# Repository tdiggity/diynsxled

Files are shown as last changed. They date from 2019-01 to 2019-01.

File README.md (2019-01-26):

# diynsxled

DIY LEDS for your NSX

# Prerequisites
1. A 3D printer is required to print the brackets and enclosure
2. A custom PCB can be made for about $30 from www.jlcpcb.com
3. [Install Arduino IDE](https://www.arduino.cc/en/Guide/HomePage)
4. Some soldering experience, or watch a few youtube videos first :)
5. Read this guide three times or more. There's a lot of info and if you're confused, open an issue above and I will try to help you out.

# Risks
The NSX taillights are old, and so there is a real risk that you'll break something. The bolts that connect to the car are fragile, the acrylic lenses are prone to cracking, etc. Just know that it's a real possibility that something can go wrong. Proceed at your own risk. 

Playing with high amperage is dangerous! Both tail lights on at full red brightness can use 5A. If you use White, even more. 

# Reading (optional)
* [NeoPixels UberGuide](https://learn.adafruit.com/adafruit-neopixel-uberguide/the-magic-of-neopixels)
* [Arduino bootloader](https://learn.sparkfun.com/tutorials/installing-an-arduino-bootloader/all) for instant start up time.

# 10,000 foot summary

The instructions below can be a bit overwelming. The high level steps are as follows:

1. Gather all the components, 3d printed parts and pcb.
2. Open tail lights and make cuts for led panels
3. Solder the pcb components
4. Wire the led together
5. Test led wiring
6. Wiring Harness - Car to PCB
7. Wiring Harness - PCB to LED Panels
8. Put brackets and leds in tail light
9. Test before sealing with car's wiring
10. Seal tail lights
11. Connect wiring

# Components

The component list links to websites for the number of items you would need to order. They are usually in sold in bundles and I have also listed the actual qty needed (if different) in case you can source these parts individually. For example, you need 6 diodes, but they only sell them in packs of 20.

If you're familiar with digikey and mouser, you can order a lot of these parts from there, too. However, some things were more expensive. 

### Custom Components
* Download the gerber zip file and send it to www.jlcpcb.com to get made. You get 10 for the same price, good if you mess up or for a group buy.
* Print the 3D printed parts in the `stl/` directory.
  * For tail light pieces, only drivers side is included. Use your slicer to mirror the brake and turn signal brackets for the passenger side. The reverse light bracket can be used on either side.
  * The parts are easy to print and do not require supports or anything special. 
  * Print with ABS. PETG should work, but ABS if you can.
  * In your slicer, split the parts up for the enclosure and print individually (and for bulb mount if using that).

### Amazon
* When installing LEDs, you'll get fast blinking turnsignals unless you use load resistors or the bulb sockets (both are listed as optional, pick one if you want regular speed blinking).
* The AVR programmer is optional, explained later on, but allows the Arduino to be programmed to wake up instantly without delay. 

|  Component | QTY | Actual QTY items needed | Notes |
| --- | --- | --- | --- |
|  [Pololu 5v regulator](https://www.amazon.com/Pololu-Step-Down-Voltage-Regulator-D24V90F5/dp/B01IGGR6TW?tag=diynsxled-20) | 1 |  |  |
|  [5mm terminals 2/3P pack](https://www.amazon.com/Gikfun-Terminal-Connector-Arduino-EK8365/dp/B015E3O4GS?tag=diynsxled-20) | 1 | 6x2pin, 2x3pin |  |
|  [2.5mm terminals 3P pack](https://www.amazon.com/Simpo-Terminal-300v10a-Drawing-Drawing/dp/B018OTAKJO?tag=diynsxled-20) | 1 | 28 |  |
|  [Capacitor](https://www.amazon.com/gp/product/B01DYJEHZ2?tag=diynsxled-20) | 1 |  |  |
|  [5A diode](https://www.amazon.com/gp/product/B079KCWPWQ?tag=diynsxled-20) | 1 | 6 |  |
|  [Resistors](https://www.amazon.com/gp/product/B072BL2VX1?tag=diynsxled-20) | 1 | 2x465, 5x4.7k, 5x1k |  |
|  [18ga Wire red](https://www.amazon.com/gp/product/B000HACYOS?tag=diynsxled-20) | 1 | optional if you have wire |  |
|  [18 ga Wire black](https://www.amazon.com/gp/product/B003J699RW?tag=diynsxled-20) | 1 | optional if you have wire |  |
|  [18 ga Wire green](https://www.amazon.com/gp/product/B003J65A84?tag=diynsxled-20) | 1 | optional if you have wire |  |
|  [18 ga wire pack](https://www.amazon.com/gp/product/B00N51OO7Q?tag=diynsxled-20) | 1 | optional if you have wire |  |
|  [Crimp tool](https://www.amazon.com/gp/product/B00OMM4YUY?tag=diynsxled-20) | 1 | optional, use with the cycle terminal crimps |  |
|  [Plug connectors](https://www.amazon.com/gp/product/B07DB7X9R9?tag=diynsxled-20) | 1 | optional | I prefer the ones from CycleTerminal, but you can also use these.|
|  [Benchtop DC power supply](https://www.amazon.com/gp/product/B071RNT1CD?tag=diynsxled-20) | 1 | optional, great for testing with or use a spare car battery |  |
|  [Socket adapters DIP](https://www.amazon.com/QLOUNI-122Pcs-2-54mm-Sockets-Adaptor/dp/B07CJ87NVT?tag=diynsxled-20) | 1 | Optional [1x6pin, 1x16pin] | For chips from digikey |
|  [Stacking headers for Nano](https://www.amazon.com/Shield-Stacking-Header-Arduino-Pack/dp/B0756KRCFX?tag=diynsxled-20) | 1 |  |  |
|  [Arduino Nano (Brand name)](https://www.amazon.com/Arduino-A000005-ARDUINO-Nano/dp/B0097AU5OU?tag=diynsxled-20) | 1 | optional (pick this or 3rd party) | Brand name. 3rd party just as good.|
|  [Arduino Nano (china)](https://www.amazon.com/ATmega328P-Microcontroller-Board-Cable-Arduino/dp/B00NLAMS9C?tag=diynsxled-20) | 1 | optional  |  |
|  [AVR Programmer](https://www.amazon.com/gp/product/B004G54E9I?tag=diynsxled-20) | 1 | Optional |  |
|  [Turn Signal Bulbs](https://www.amazon.com/gp/product/B07DFYSM5J?tag=diynsxled-20) | 1 | Optional |  |
|  [Load resistor](https://www.amazon.com/Resistors-Signal-License-Warning-Cancellor-x/dp/B004EDF8HY/ref=sr_1_8?tag=diynsxled-20) | 1 | Optional |  |
|  [5 wire connector](https://www.amazon.com/Wago-222-415-LEVER-NUTS-Conductor-Connectors/dp/B07CN5974J?tag=diynsxled-20) | 1 | 5, optional | There are better ways to splice wires |  
|  [Morimoto Butyl](https://www.amazon.com/RetroRubber-Grade-Butyl-Headlight-Sealant/dp/B01N5PM29J?tag=diynsxled-20) | 1 |  |  |
|  [M2/M3 bolts and nuts](https://www.amazon.com/gp/product/B07CSSVRPL?tag=diynsxled-20) | 1 | 6xM2, 10xM3 |  |
|  [Jumper wires](https://www.amazon.com/gp/product/B005TZJ0AM?tag=diynsxled-20) | 1 | optional | These will make wiring the panels together easier. We only need the short 4.7in ones.. |

**Note that the Amazon links have an affiliate link attached to them. This helps me recoupe some of the cost of development, and future dev work.* 

### Digikey
|  Component | QTY Needed | Actual items needed | Notes |
| --- | --- | --- | --- |
|  [Pin headers for Pololu regulator](https://www.digikey.com/products/en?mpart=TSW-202-07-T-S&v=612) | 2 |  |  |
|  [Opto 4ch](https://www.digikey.com/product-detail/en/PS2501-4-A/PS2501-4A-ND/770687) | 1 |  |  |
|  [Opto 2ch](https://www.digikey.com/product-detail/en/4N35/4N35-ND/1738522) | 1 |  |  |

### Aliexpress
* The LED panels are cheapest on Aliexpress. With regards to quality issues, I feel that all the panels i've bought have for the most part been great. Only 2 died on me, and I think that had more to do with me than them. In any case, purchasing extras might be good insurance since they take awhile to ship. 
* In total, you need 14 panels, 65mm square. The name branded NeoPixel panels from AdaFruit are 71mm.....do not use those unless you want to update the STL files.
* The White panels are used for the reverse light area. You can opt to use all black led panels, too.

|  Component | QTY Needed | Actual items needed | Notes |
| --- | --- | --- | --- |
|  [White LED panels](https://www.aliexpress.com/item/WS2812B-8x8-64-Bit-Full-Color-5050-RGB-LED-Lamp-Panel-Light-for-Arduino-OS857/32822265747.html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) | 2 |  |  |
|  [Black LED panels](https://www.aliexpress.com/item/WS2812-LED-5050-RGB-8x8-64-LED-Matrix-for-Arduino/32622872541.html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) | 12 |  |  |

### Cycle Terminal
These connectors connect to the OEM connectors for a really clean install. The optional parts are used in place of using a bulb socket adapter to wire things up. This is explained later on, but I recommend getting these optional components because it makes things more compact. 

|  Component | QTY Needed | Actual items needed | Notes |
| --- | --- | --- | --- |
|  ET250-4 Male | 1 |  | (OEM Acc power) |
|  HD 090-2 Male | 2 |  | (OEM Turn signal) |
|  HD 090-8 Male | 1 |  | (OEM main wiring) |
|  HD 090-6 Female | 1 |  | (OEM brake lamp defeat) |
|  3 pin HD 090  Female Connector | 6 | Optional | (data lines) |
|  3 pin HD 090  Male Connector | 6 | Optional | (data lines) |
|  2 pin HD 090  Female Connector | 4 | Optional | (power lines) (same as TS) (voltage drop) |
|  2 pin HD 090  Male Connector | 4 | Optional | (voltage drop) |

# Opening up your tail lights
Search google for opening up your tail light housing. You'll need to remove the gasket and electrical wiring and brake lamp detector box. 

# Tail Light Prep
You need to make these cuts to your tail lights. They are not visible if you decide to revert back to stock:

1. In the brake light area, there is a strip of plastic that comes flush to the rest of the light. This needs to be cut down. 
2. Next to the strip that you just cut, you'll need to make a small hole for the screw terminal to fit through. Save this step for when you test fit the 3d printed brackets and leds. 
3. Reverse light area, make two cuts so let the led panel sit flush.
tbd - include images of cuts

Next:
1. Remove the reflectors in the brake, reverse, and turnsignal areas.
2. You can keep all the diffusers.
3. you will not reuse the inner clear panel that is on the brake lamp area.

# LED Panel Prep
### soldering
Solder the two 3-pin 2.54mm terminals to each panel. 
tbd - image

### panel orientation and prep
The order of the panels goes from reverse light to brake lights to turn signals.
1 reverse light panels
5 brake lights panels
1 turn signal panels

For the 5 brake light panels, you need to glue the ends together. Each panel has an input terminal and output terminal. You want to glue them together so that the output terminal of one panel is next to the input terminal of another. 

tbd see image

# PCB Soldering

The holes will guide you. If it doesn't fit, you have the wrong part. 

Misc notes:
1. 5mm pins are used with the biggest holes in the voltage regulator. Only the center two on each end need to be soldered. 
2. The DIP sockets on the two chips are optional, but allow you to change the chips out if they get damaged without having to desolder everything. 
3. The nano uses header pins to easy connect and disconnect. There are 15 pins on each side. On my board, I only had 14 pin stacking headers, so my last row of pins near the usb is not used but that's ok because no connections are there. 
4. PCB uses M2 screws to mount to enclosure. 

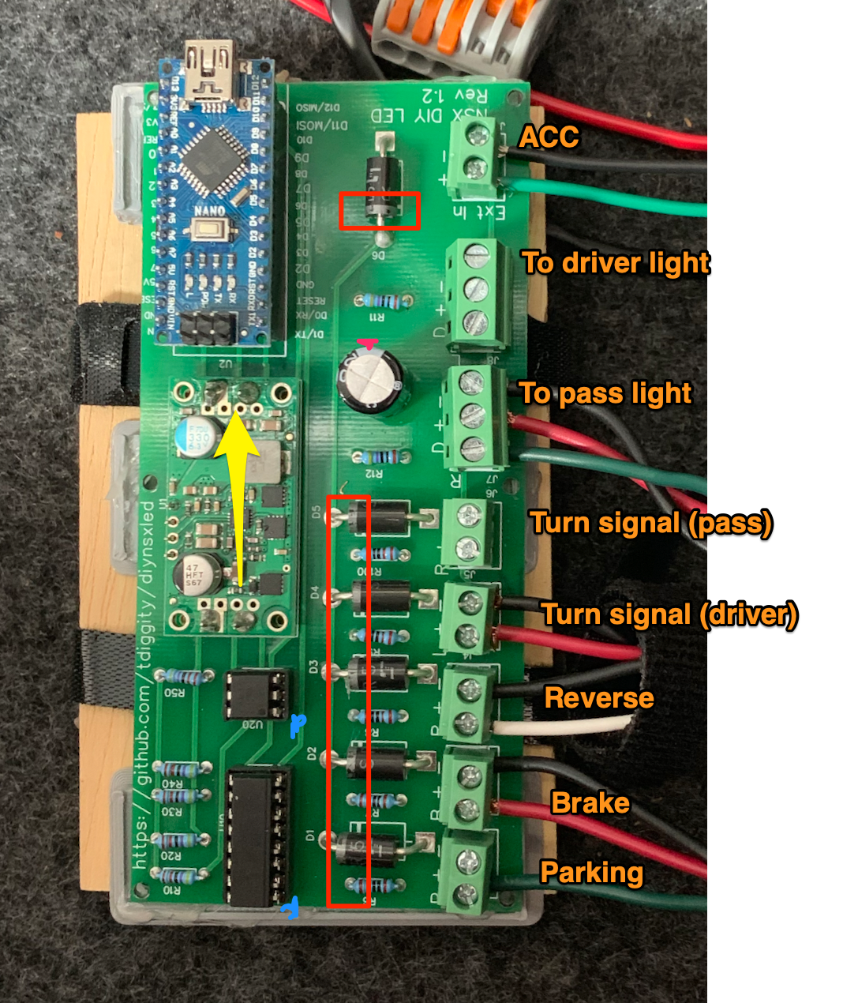
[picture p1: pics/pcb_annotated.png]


Notes about image:
* Red boxes - Diode orientation matters
* Red dot - Note grey strip on capacitor
* Blue dots - These note pin 1 of the chip, usually a notch or dot on the chip
* Yellow arrow - Voltage In to Voltage Out

tbd - insert resistor diagram here
Resistors
* 465 ohm - R11, R12
* 1k ohm - R10, 20, 30, 40, 50
* 4.7k ohm - R6, R7, R8, R9, R100

# Wiring guide
## LED panels
tbd
* Note, the white panels are labeled backwards, probably!

## PCB to LEDs
tbd 
## Car to PCB
tbd

# Test fit parts in tail lights
Test mount the 3d printed brackets in the tail light with the led panels. Ensure that the panels fit flush. They should slide in easily. If not, you might need to shave off some more of the cuts you previously made. 

If everything fits, first glue the 3d printed brackets to the tail lights with some superglue and/or hot glue. Once that sets, use hotglue on the tabs and attach the led panels. Super glue and hot glue don't conduct electricity.

Tip: Ensure that the brackets are flush with the border of the tail lights. Hot glue sets quickly enough for you to get them  lined up well. 

# Loading the arduino code
For testing - open the test file in the `test/` folder and upload it using the arduino IDE. 
For driving use - open the diynsxled.ino file and upload it using the arduino IDE. 

### Advanced - use the AVR programmer to load the code
The Arduino is only on when the key is in ACC position (2nd key position and also when engine is on). Otherwise it is off and not using any power.

In stock form, it takes about 1-2 seconds before any code can be run when first powering up. WHen the car is running, the Arduino is always on, so there is no worry of delay. 

When the Arduino is off, the LEDS will not work correctly in certain cases because the arduino does not have power long enough to get past the startup stage:
* When the emergency lights are on
* If you have a security system that blinks the leds upon activation/deactivation. 

This can be fixed by using an [AVR programmer](https://www.amazon.com/gp/product/B004G54E9I?tag=diynsxled-20) to remove the 1-2 second delay and instantly execute the LED program. Follow the instructions here: [AVR Guide](https://learn.sparkfun.com/tutorials/pocket-avr-programmer-hookup-guide/all) (pay attention to the "Programming with Arduino" section.)

# Testing (pre-flight)
Load the test code in the `tests/` folder. The first time you run the test code, let them run for a few hours or overnight. If you're using the [Benchtop DC power supply](https://www.amazon.com/gp/product/B071RNT1CD?tag=diynsxled-20), this won't be a problem. If using a car battery, i'm not sure how long they will last. But something is better than nothing. It's been said that if an electrical thing will fail, it'll fail earlier rather than later. 

It's advised to do testing at various stages to check your wiring:
* After all terminals and wires soldered, but before glueing panels together
* After brake panels are glued together
* After mounting into taillights but before sealing
* After sealing

# Sealing your lights
Use morimoto butyl

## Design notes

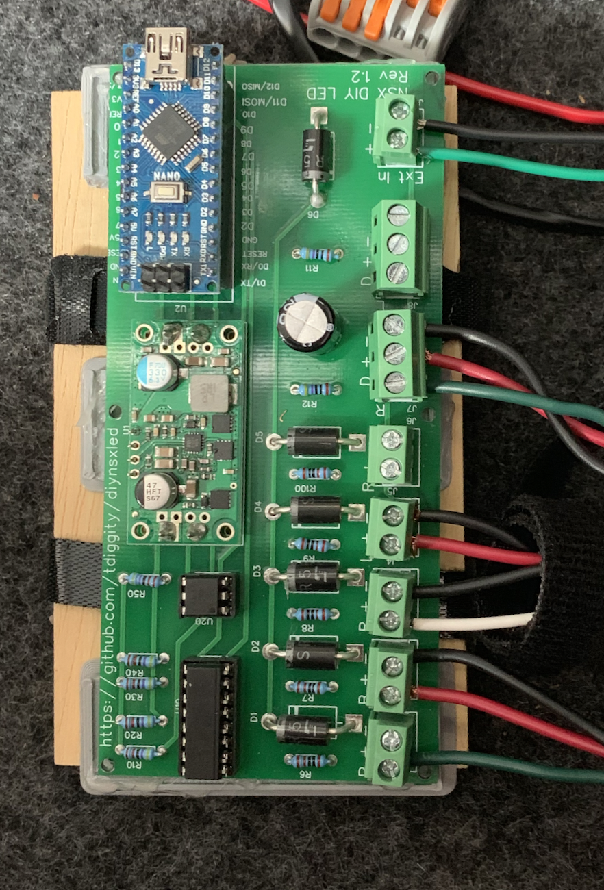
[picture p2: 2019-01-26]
pics/pcb.png

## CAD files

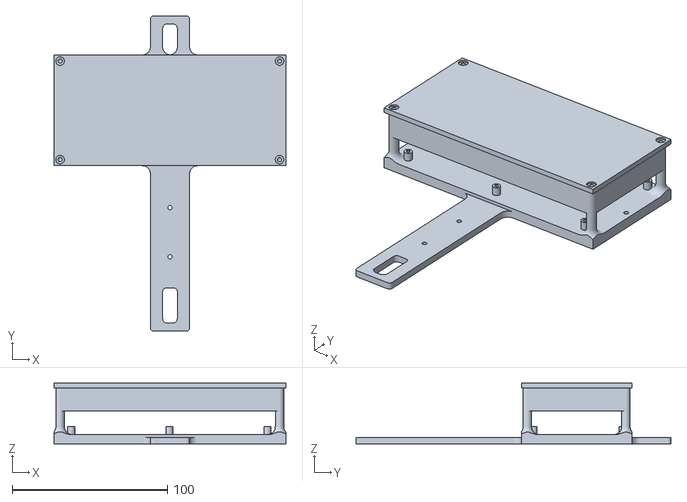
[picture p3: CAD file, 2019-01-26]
stls/enclosure/enclosure_plus_bracket.stl
149.5 x 203.0 x 39.0

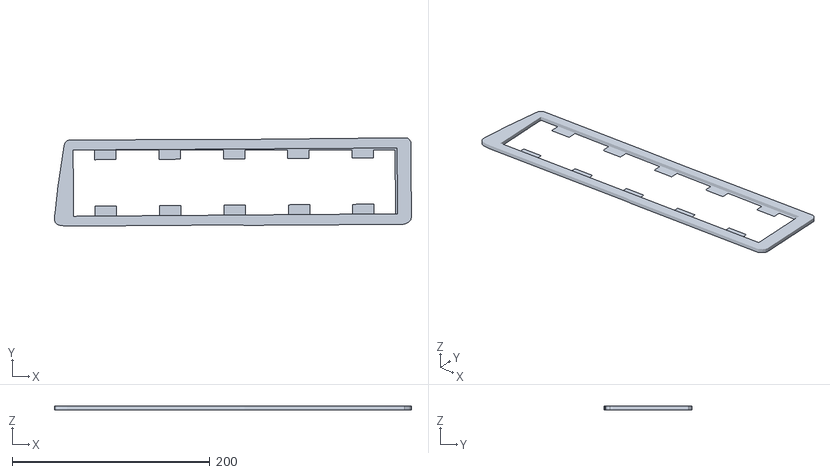
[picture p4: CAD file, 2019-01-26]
stls/taillights/Tail Lights - Brake Lights (Driverside).stl
361.5 x 89.5 x 4.00

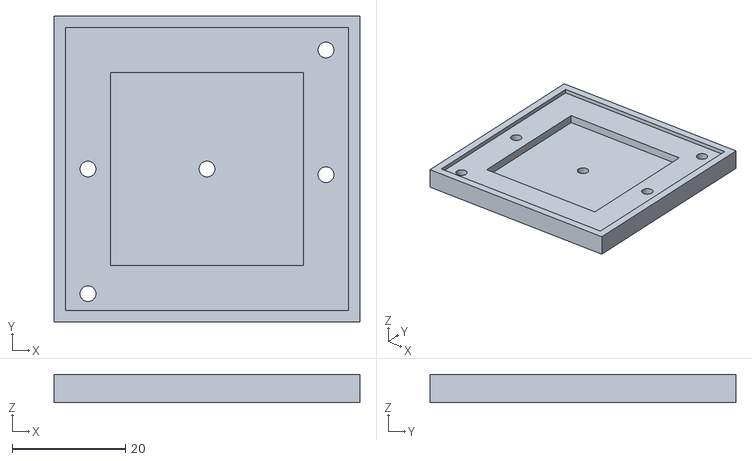
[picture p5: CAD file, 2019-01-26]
stls/enclosure/load_resistor_mount.stl
54.0 x 54.0 x 5.00

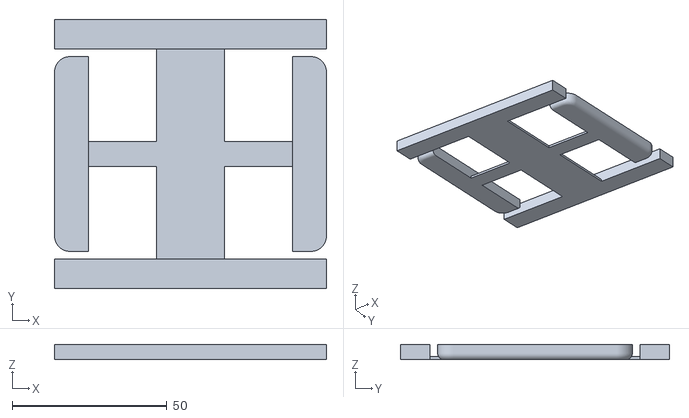
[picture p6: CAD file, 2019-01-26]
stls/taillights/Reverse Light.stl
88.0 x 87.0 x 5.00

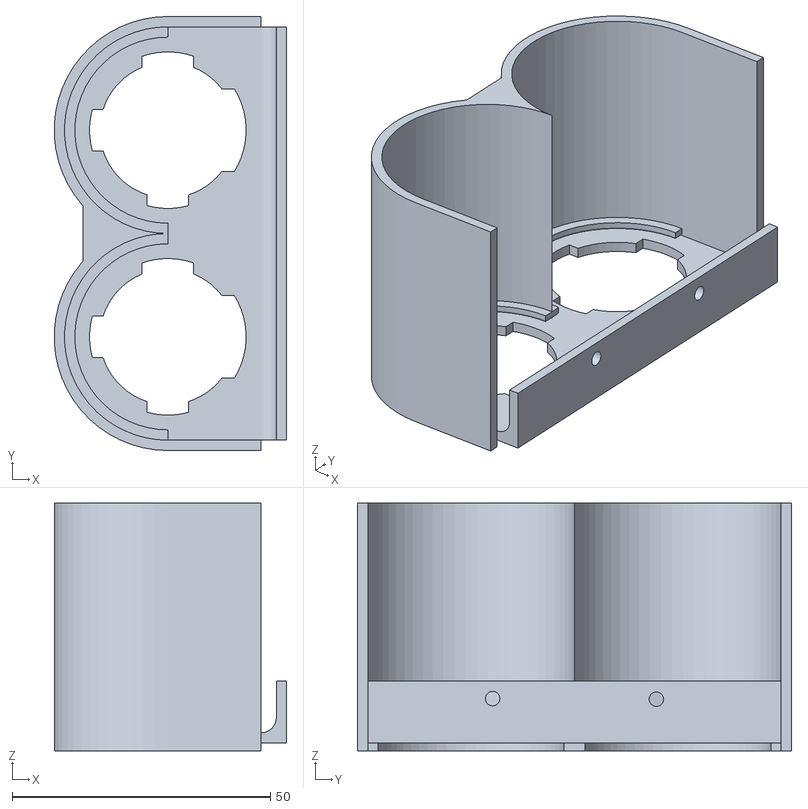
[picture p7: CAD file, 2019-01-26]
stls/enclosure/bulb_mount.stl
45.0 x 84.0 x 48.0

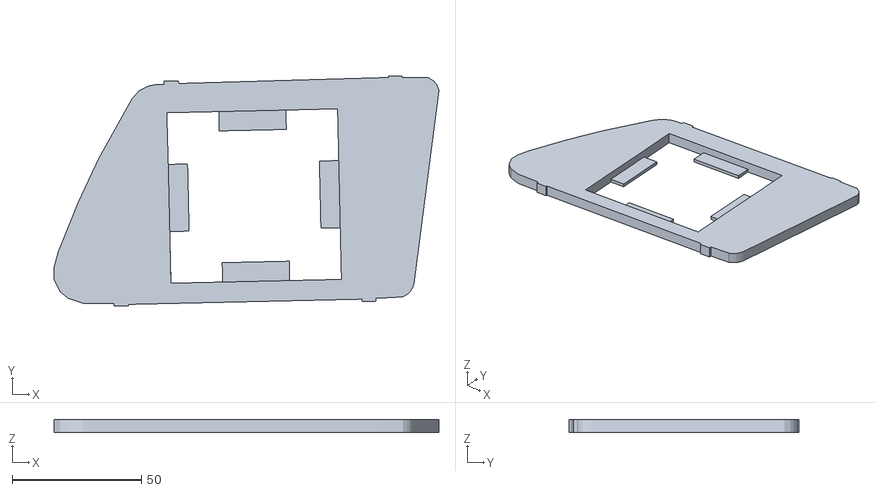
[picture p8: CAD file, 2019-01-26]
stls/taillights/Turn signal (Drivers side).stl
149.0 x 89.1 x 5.00

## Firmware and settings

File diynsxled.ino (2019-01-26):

/*
   LED Tail lights for NSX
   All rights reserved
   Intended for off-road use only
*/

#include <Adafruit_GFX.h>
#include <Adafruit_NeoMatrix.h>
#include <Adafruit_NeoPixel.h>
#include <MemoryFree.h>
#ifndef PSTR
#define PSTR // Make Arduino Due happy
#endif

// Data output pins
#define PASSENGER_MATRIX_PIN  5   // passenger side
#define DRIVER_MATRIX_PIN     6   // passenger side

// Opto-isolator inputs
#define OPTO_IN_PARKING       7   // parking
#define OPTO_IN_BRAKES        8   // brakes
#define OPTO_IN_REVERSE       9   // reverse
#define OPTO_IN_DRIVER_TS     10  // driver turn signal
#define OPTO_IN_PASSENGER_TS  11  // passenger turn signal

// Color definitions - only used for black because you can't set
// brightness on these without changing them all.
#define BLACK    0x0000
#define RED      0xF800
#define ORANGE   0xFC60
#define WHITE    0xFFFA
#define BLUE     0x001F

// brightness_levels
#define BRAKE_BRIGHTNESS    220
#define PARKING_BRIGHTNESS  125
#define TS_BRIGHTNESS       220
#define REVERSE_BRIGHTNESS  125

// default state of optocoupler inputs
int pinState_driver_ts = 0;
int pinState_passenger_ts = 0;
int pinState_reverse = 0;
int pinState_parking = 0;
int pinState_brake = 0;

// for determining what leds to turn on
boolean brakesOn = false;
boolean parkingOn = false;
boolean driverTurnsignalOn = false;
boolean passengerTurnsignalOn = false;
boolean reverseOn = false;

void setup() {
  pinMode(OPTO_IN_PARKING,      INPUT_PULLUP);
  pinMode(OPTO_IN_BRAKES,       INPUT_PULLUP);
  pinMode(OPTO_IN_REVERSE,      INPUT_PULLUP);
  pinMode(OPTO_IN_DRIVER_TS,    INPUT_PULLUP);
  pinMode(OPTO_IN_PASSENGER_TS, INPUT_PULLUP);
  pinMode(LED_BUILTIN,          OUTPUT);        // turn on if there's an error
  //Serial.begin(115200);
  Serial.println("starting");
}

void loop() {
  // get state of what lights should be on
  pinState_parking      = digitalRead(OPTO_IN_PARKING);
  pinState_brake        = digitalRead(OPTO_IN_BRAKES);
  pinState_reverse      = digitalRead(OPTO_IN_REVERSE);
  pinState_driver_ts    = digitalRead(OPTO_IN_DRIVER_TS);
  pinState_passenger_ts = digitalRead(OPTO_IN_PASSENGER_TS);
  delay(1); // delay in between reads for stability

  Serial.print("freeMemory()=");
  Serial.println(freeMemory());

  // analyze the state of lights
  // brake lights take priority over parking lights.
  if (pinState_brake == 1) {
    brakesOn = true;
    parkingOn = false;
  } else if (pinState_parking == 1) {
    parkingOn = true;
    brakesOn = false;
  } else {
    brakesOn = false;
    parkingOn = false;
  }

  //reverse lights
  if (pinState_reverse == 1) {
    reverseOn = true;
  } else {
    reverseOn = false;
  }

  //left turnsignal
  if (pinState_driver_ts == 1) {
    driverTurnsignalOn = true;
  } else {
    driverTurnsignalOn = false;
  }
  
  //right turnsignal
  if (pinState_passenger_ts == 1) {
    passengerTurnsignalOn = true;
  } else {
    passengerTurnsignalOn = false;
  }


  // we do it this way because there isn't enough memory if you make the neopixels global.
  setLeds(brakesOn, parkingOn, reverseOn, passengerTurnsignalOn, PASSENGER_MATRIX_PIN);
  setLeds(brakesOn, parkingOn, reverseOn, driverTurnsignalOn, DRIVER_MATRIX_PIN);
}

void setLeds(boolean brakesOn, boolean parkingOn, boolean reverseOn, boolean turnsignalOn, 
              int pin) {

  unsigned long startTime = millis();
  // Matrix objects
  Adafruit_NeoMatrix matrix = Adafruit_NeoMatrix(
                                8, 8, // pixel width/height per matrix
                                7,    // number of tiles
                                1,    // width of tiles
                                pin,
                                NEO_MATRIX_TOP     + NEO_MATRIX_LEFT +
                                NEO_MATRIX_ROWS    + NEO_MATRIX_PROGRESSIVE,
                                NEO_GRB            + NEO_KHZ800);
  matrix.begin(); // init matrix
  
  if (brakesOn) {
    // only show 2 beause that's how stock setup does it
    //matrix.fillRoundRect(8,  0, 12, 8, 1, matrix.Color(BRAKE_BRIGHTNESS, 0, 0));
    matrix.fillRoundRect(22, 0, 12, 8, 1, matrix.Color(BRAKE_BRIGHTNESS, 0, 0));
    matrix.fillRoundRect(36, 0, 12, 8, 1,matrix.Color(BRAKE_BRIGHTNESS, 0, 0));
  } else if(parkingOn) {
    matrix.fillRoundRect(8,  0, 12, 8, 1, matrix.Color(PARKING_BRIGHTNESS, 0, 0));
    matrix.fillRoundRect(22, 0, 12, 8, 1, matrix.Color(PARKING_BRIGHTNESS, 0, 0));
    matrix.fillRoundRect(36, 0, 12, 8, 1, matrix.Color(PARKING_BRIGHTNESS, 0, 0));
  }

  if (reverseOn) {
    matrix.fillRect(0, 0, 8, 8, matrix.Color(REVERSE_BRIGHTNESS, REVERSE_BRIGHTNESS, REVERSE_BRIGHTNESS));
  }

  if (turnsignalOn) {
    matrix.fillRoundRect(48, 0, 8, 8, 1, matrix.Color(TS_BRIGHTNESS, 0, 0));
  }

  matrix.show();
  Serial.print("P ");
  Serial.print(parkingOn);
  Serial.print(" B ");
  Serial.print(brakesOn);
  Serial.print(" R ");
  Serial.print(reverseOn);
  Serial.print(" TS ");
  Serial.print(turnsignalOn);
  Serial.print(" PIN ");
  Serial.print(pin);
  Serial.print(" Matrix: freeMemory()=");
  Serial.print(freeMemory());
  unsigned long currentTime = millis();
  unsigned long elapsedTime = currentTime - startTime;
  Serial.print("\t Time to calculate: ");
  Serial.println(elapsedTime);

  // if it takes more than 100ms to calculate what leds to show, then turn on the led!
  if (elapsedTime > 100) {
    digitalWrite(LED_BUILTIN, HIGH);
  }
}

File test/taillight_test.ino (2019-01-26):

/*
 * Test code for DIYNSXLED
 * Use with one side only
 * Insert the 3 wires into the passenger out
 * Add power to the ACC 2-pin port
 * Run this code and it will cycle through the lights in this order: Parking, brake, reverse, turn signal.
 */

#include <Adafruit_GFX.h>
#include <Adafruit_NeoMatrix.h>
#include <Adafruit_NeoPixel.h>
#ifndef PSTR
  #define PSTR // Make Arduino Due happy
#endif

// Data output pins
#define PASSENGER_MATRIX_PIN  5   // passenger side

// Opto-isolator inputs
#define OPTO_IN_PARKING       7   // parking
#define OPTO_IN_BRAKES        8  // brakes
#define OPTO_IN_REVERSE       9  // reverse
#define OPTO_IN_PASSENGER_TS  10  // passenger turn signal

// Color definitions - only used for black because you can't set 
// brightness on these without changing them all. 
#define BLACK    0x0000
#define RED      0xF800
#define ORANGE   0xFC60
#define WHITE    0xFFFA
#define BLUE     0x001F

// brightness_levels
#define BRAKE_BRIGHTNESS    220
#define PARKING_BRIGHTNESS  100
#define TS_BRIGHTNESS       220
#define REVERSE_BRIGHTNESS  100

// default state
int pinState_passenger_ts = 0;
int pinState_reverse = 0;
int pinState_parking = 0;
int pinState_brake = 0;

// Matrix objects
Adafruit_NeoMatrix passenger_matrix = Adafruit_NeoMatrix(
  8, 8, // pixel width/height per matrix
  7,    // number of tiles
  1,    // width of tiles
  PASSENGER_MATRIX_PIN,
  NEO_MATRIX_TOP     + NEO_MATRIX_LEFT +
  NEO_MATRIX_ROWS    + NEO_MATRIX_PROGRESSIVE,
  NEO_GRB            + NEO_KHZ800);

void setup() {
  pinMode(OPTO_IN_PARKING,      INPUT_PULLUP);
  pinMode(OPTO_IN_BRAKES,       INPUT_PULLUP);
  pinMode(OPTO_IN_REVERSE,      INPUT_PULLUP);
  pinMode(OPTO_IN_PASSENGER_TS, INPUT_PULLUP);
  passenger_matrix.begin();
  passenger_matrix.show();
}

void loop() {
//  pinState_parking      = digitalRead(OPTO_IN_PARKING);
//  pinState_brake        = digitalRead(OPTO_IN_BRAKES);
//  pinState_reverse      = digitalRead(OPTO_IN_REVERSE);
//  pinState_passenger_ts = digitalRead(OPTO_IN_PASSENGER_TS);
//  delay(1); // delay in between reads for stability

  // parking and brake lights
  // brake lights take priority over parking lights.

  // brakes
  setParkingMatrix(PARKING_BRIGHTNESS);
  passenger_matrix.show();
  delay(2000);
  resetBrakes();

  setBrakeMatrix(BRAKE_BRIGHTNESS);
  passenger_matrix.show();
  delay(2000);
  resetBrakes();

  setReverse(REVERSE_BRIGHTNESS);
  passenger_matrix.show();
  delay(2000);
  resetReverse();
  
  setTurnSignal(TS_BRIGHTNESS);
  passenger_matrix.show();
  delay(2000);
  resetTurnSignal();
  
}

void setBrakeMatrix(int brightness) {
  // remove first one to match oem
  //passenger_matrix.fillRoundRect(8,  0, 12, 8, 1, passenger_matrix.Color(brightness, 0, 0));
  passenger_matrix.fillRoundRect(22, 0, 12, 8, 1, passenger_matrix.Color(brightness, 0, 0));
  passenger_matrix.fillRoundRect(36, 0, 12, 8, 1, passenger_matrix.Color(brightness, 0, 0));
}
// 0, 8, 16, 24, 32, 40, 48
// 8+12 = 20    8 to 20
// 2 gap
// 22+12 = 36   22 to 34
// 2 gap
// 38+12 = 50   36 to 48


void setParkingMatrix(int brightness) {
  passenger_matrix.fillRoundRect(8,  0, 12, 8, 1, passenger_matrix.Color(brightness, 0, 0));
  passenger_matrix.fillRoundRect(22, 0, 12, 8, 1, passenger_matrix.Color(brightness, 0, 0));
  passenger_matrix.fillRoundRect(36, 0, 12, 8, 1, passenger_matrix.Color(brightness, 0, 0));
}

void resetBrakes() {
  passenger_matrix.fillRect(8, 0, 40, 8, BLACK);
}

void setReverse(int brightness) {
  passenger_matrix.fillRect(0, 0, 8, 8, passenger_matrix.Color(brightness, brightness, brightness));
}

void resetReverse() {
  passenger_matrix.fillRect(0, 0, 8, 8, BLACK);
}

void setTurnSignal(int brightness) {
  passenger_matrix.fillRect(48, 0, 8, 8, passenger_matrix.Color(brightness, 0, 0));
}

void resetTurnSignal() {
  passenger_matrix.fillRect(48, 0, 8, 8, BLACK);
}

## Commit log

2018-10-30 adding gerber files
2018-11-02 Change data pin
2018-12-30 Turn on built in LED if it takes too long
    [diynsxled.ino]
2019-01-02 change pin for passenger turn signal
2019-01-04 Code for driver side tail lights
2019-01-04 Update gerber file
2019-01-26 Tnguyen/stls (#4)
    * STL files
    * update gitignore
    [Reverse Light.stl, Tail Lights - Brake Lights (Driverside).stl, Turn signal (Drivers side).stl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]
